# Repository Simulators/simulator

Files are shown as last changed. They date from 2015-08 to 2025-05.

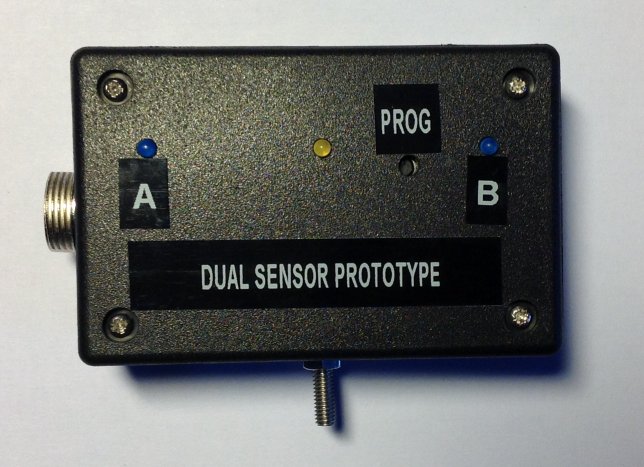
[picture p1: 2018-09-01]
experimental/twinsensor/documentation/Images/Img_0275.jpg

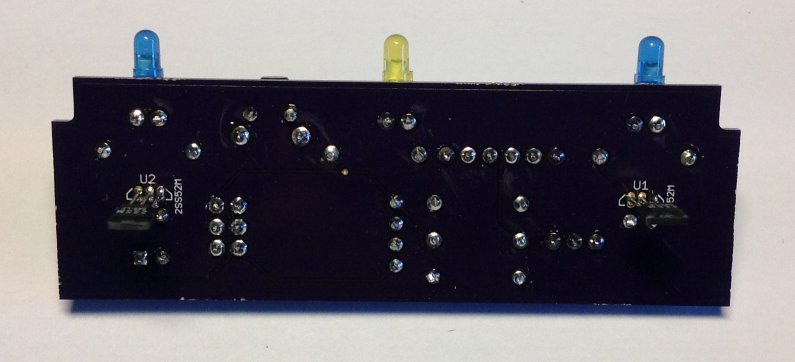
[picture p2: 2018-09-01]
experimental/twinsensor/documentation/Images/Img_0268 (1).jpg

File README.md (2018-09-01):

# simulator
The Liverpool Ringing Simulator Project

<b>The Type 1 simulator is no longer under active development. The repository for the Type 2 simulator is at https://github.com/Simulators/simulator-type2, and you should start there if you are building a new simulator.</b>

Here you will find archived all the resources for building the Liverpool Ringing Simulator Project's original (Type 1) simulator interfaces and sensor heads, including:
* Hardware & Software Manuals
* Firmware Source Code
* Eagle PCB Designs
* PCB Fabrication Gerber Files

If you didn't get here from http://www.simulators.org.uk/, you might want to go and look at that, too.

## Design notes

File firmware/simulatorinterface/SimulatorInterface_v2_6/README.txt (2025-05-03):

*********************************************************************************************
*                 HOW TO USE OPTION X - TURNING OFF DELAYS IN THE INTERFACE                 *
*********************************************************************************************

Type 1 Simulator Interface firmware v2.6 implements a feature to turn off the application of
strike delays in the Simulator Interface, i.e. to use the Type 2 behaviour where delays are
managed within the Simulator Software itself (e.g. Abel).

This feasture has been developed for one particular use case. For most Type 1 users, firmware
v2.5 is still the latest recommended version.

           *** THIS FEATURE DOES NOT APPEAR IN THE TYPE 1 SIMULATOR DOCUMENTATION ***

By default, a Type 1 interface stores and applies the strike delay (from BDC to strike point)
in the interface, receiving the delays from Abel at startup and saving them to EEPROM. CLI
option X turns this off, so that signals are sent to the PC at BDC, not at the strike point,
which is the Type 2 behaviour. To support this, the WAIT_TO_SEND state does double duty
as the post-signal guard timer. 

When application of delays in the interface is turned off, the option to set default timers
(Option Z in Debug Mode) is changed to set to 100ms, the default Type 2 Guard Timer, instead
of 500ms, and saving to EEPROM (Option S) is changed to save the delay timers to EEPROM along
with the other settings. The serial receiver code is also changed to not overwrite the timers
when application of delays is turned off.

To disable application of delay timers in the interface, do the following:
 * Select CLI Option X to toggle the applyDelayTimers flag to FALSE.
 * Select CLI Option D to enable debugging.
 * Select CLI Option Z to set 100ms (10cs) timers.
 * Select CLI Option S to save all this to EEPROM.
 * Reboot the interface with the reset button.
 * Change the Abel configuration to check the box "Abel applies delays (No MBI)".
 
Strike delays will now be applied by Abel, and any delay values sent to the interface will be ignored.

To re-enable application of delay timers in the interface, do the following:
 * Select CLI Option X to toggle the applyDelayTimers flag to TRUE.
 * Select CLI Option S to save this change to EEPROM.
 * Reboot the interface with the reset button.
 * Change the Abel configuration to uncheck the "Abel applies delays (No MBI)" box, and restart Abel.

Abel will now send delay values to the interface, which will store and apply them.

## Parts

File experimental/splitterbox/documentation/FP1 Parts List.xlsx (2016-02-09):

Splitter Box Functional Prototype - Main Parts List
 | Part | Qty | Farnell
 | USB-B-S-RA | 6 | 2112373
 | FT232RL | 6 | 1146032
 | 47pF 2.54mm 50V MLCC | 12 | 1141762
 | 10K | 14 | 9341110
 | 1K | 7 | 9341102
 | LED 3mm Blue | 6 | Ebay
 | 100nF 2.54mm 50V MLCC | 10 | 1457655
 | MAX233EPP+G36/MAX233CPP+G36 | 1 | 2085180 | or 2113688 (not low temp)
 | ATmega328P-PU | 1 | 1715487
 | IC Socket 20 pin | 1 | 2445624
 | IC Socket 28 pin | 1 | 2445626
 | 47uF 2.54mm 25V 6.3mm Elko | 1 | 1870939
 | Omrom PB B3F-1020 | 2 | 1608274
 | BiColor LED 3mm Red/Green 2 Lead | 1 | 1142488 | Prototype was 1581204, now discontinued
 | 10nF 2.54mm 50V MLCC | 1 | 1141772
 | Ferrite BL02RN1R2M2B | 1 | 9526838
 | 0.1" Header Pins | 12 | Ebay

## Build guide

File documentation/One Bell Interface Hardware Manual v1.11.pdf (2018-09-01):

# The Liverpool Ringing Simulator

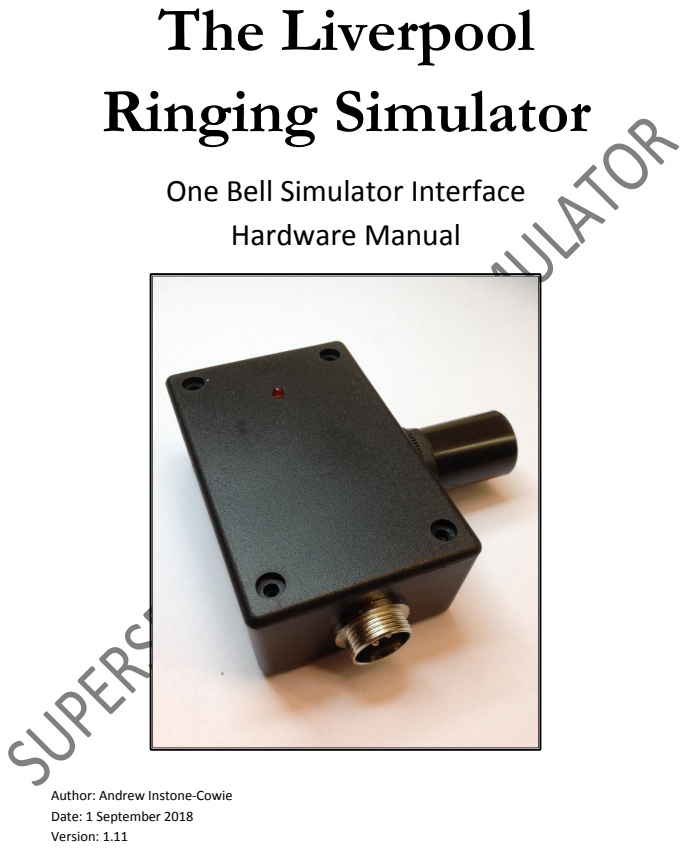
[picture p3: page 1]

One Bell Simulator Interface
Hardware Manual

Author: Andrew Instone-Cowie
Date: 1 September 2018
Version: 1.11

### Contents

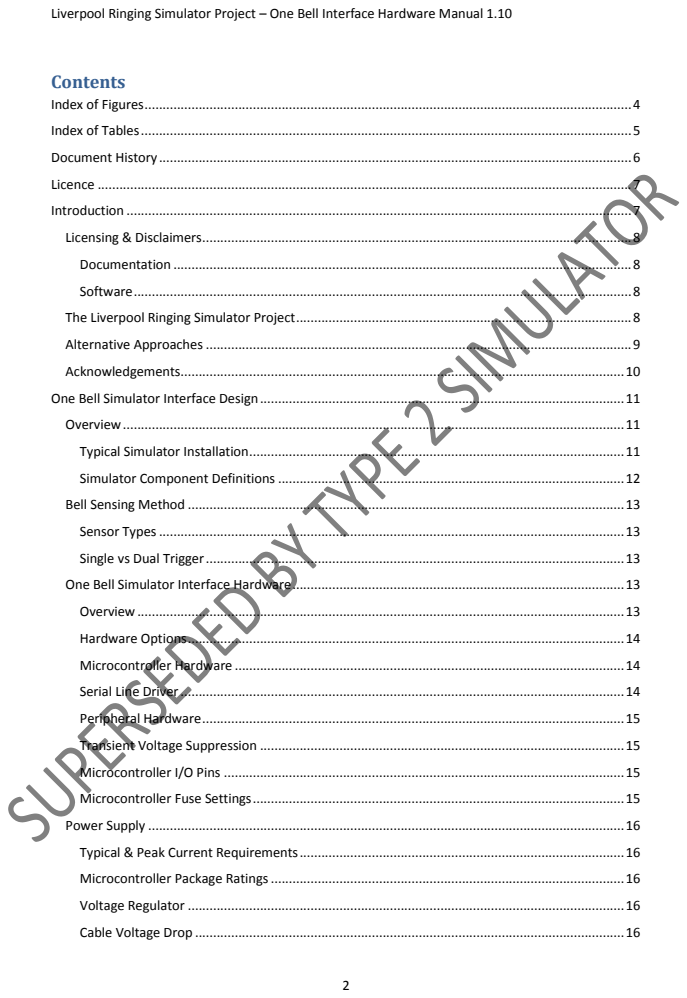
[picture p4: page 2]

Liverpool Ringing Simulator Project – One Bell Interface Hardware Manual 1.10

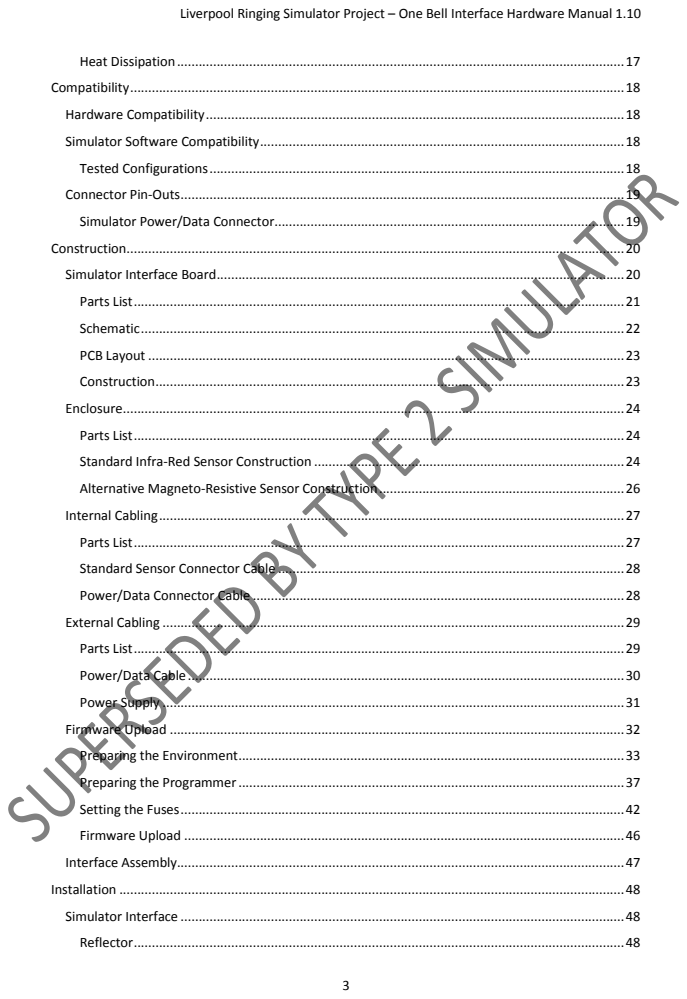
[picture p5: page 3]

### Index of Figures

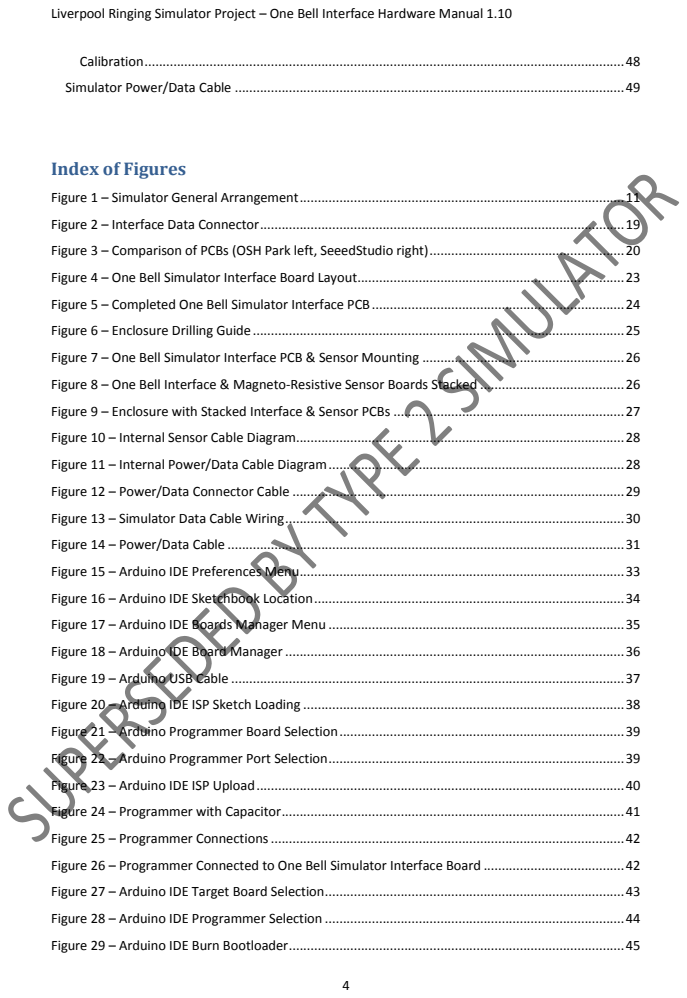
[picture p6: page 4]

Calibration.....................................................................................................................................48
Simulator Power/Data Cable ............................................................................................................49

Figure 1 – Simulator General Arrangement..........................................................................................11
Figure 2 – Interface Data Connector.....................................................................................................19
Figure 3 – Comparison of PCBs (OSH Park left, SeeedStudio right)......................................................20
Figure 4 – One Bell Simulator Interface Board Layout..........................................................................23
Figure 5 – Completed One Bell Simulator Interface PCB......................................................................24
Figure 6 – Enclosure Drilling Guide .......................................................................................................25
Figure 7 – One Bell Simulator Interface PCB & Sensor Mounting ........................................................26
Figure 8 – One Bell Interface & Magneto-Resistive Sensor Boards Stacked ........................................26
Figure 9 – Enclosure with Stacked Interface & Sensor PCBs ................................................................27
Figure 10 – Internal Sensor Cable Diagram...........................................................................................28
Figure 11 – Internal Power/Data Cable Diagram..................................................................................28
Figure 12 – Power/Data Connector Cable ............................................................................................29
Figure 13 – Simulator Data Cable Wiring..............................................................................................30
Figure 14 – Power/Data Cable ..............................................................................................................31
Figure 15 – Arduino IDE Preferences Menu..........................................................................................33
Figure 16 – Arduino IDE Sketchbook Location......................................................................................34
Figure 17 – Arduino IDE Boards Manager Menu ..................................................................................35
Figure 18 – Arduino IDE Board Manager ..............................................................................................36
Figure 19 – Arduino USB Cable .............................................................................................................37
Figure 20 – Arduino IDE ISP Sketch Loading .........................................................................................38
Figure 21 – Arduino Programmer Board Selection...............................................................................39
Figure 22 – Arduino Programmer Port Selection..................................................................................39
Figure 23 – Arduino IDE ISP Upload......................................................................................................40
Figure 24 – Programmer with Capacitor...............................................................................................41
Figure 25 – Programmer Connections..................................................................................................42
Figure 26 – Programmer Connected to One Bell Simulator Interface Board .......................................42
Figure 27 – Arduino IDE Target Board Selection...................................................................................43
Figure 28 – Arduino IDE Programmer Selection ...................................................................................44
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

### Index of Tables

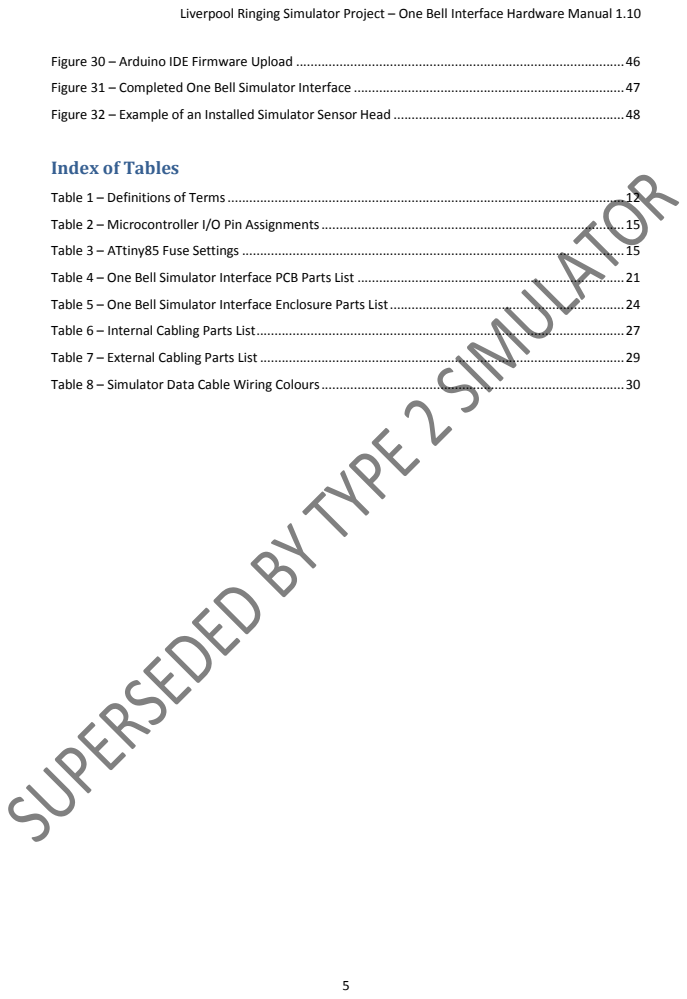
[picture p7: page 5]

Figure 30 – Arduino IDE Firmware Upload ...........................................................................................46
Figure 31 – Completed One Bell Simulator Interface ...........................................................................47
Figure 32 – Example of an Installed Simulator Sensor Head ................................................................48

Table 1 – Definitions of Terms..............................................................................................................12
Table 2 – Microcontroller I/O Pin Assignments....................................................................................15
Table 3 – ATtiny85 Fuse Settings..........................................................................................................15
Table 4 – One Bell Simulator Interface PCB Parts List ..........................................................................21
Table 5 – One Bell Simulator Interface Enclosure Parts List.................................................................24
Table 6 – Internal Cabling Parts List......................................................................................................27
Table 7 – External Cabling Parts List .....................................................................................................29
Table 8 – Simulator Data Cable Wiring Colours....................................................................................30

### Document History

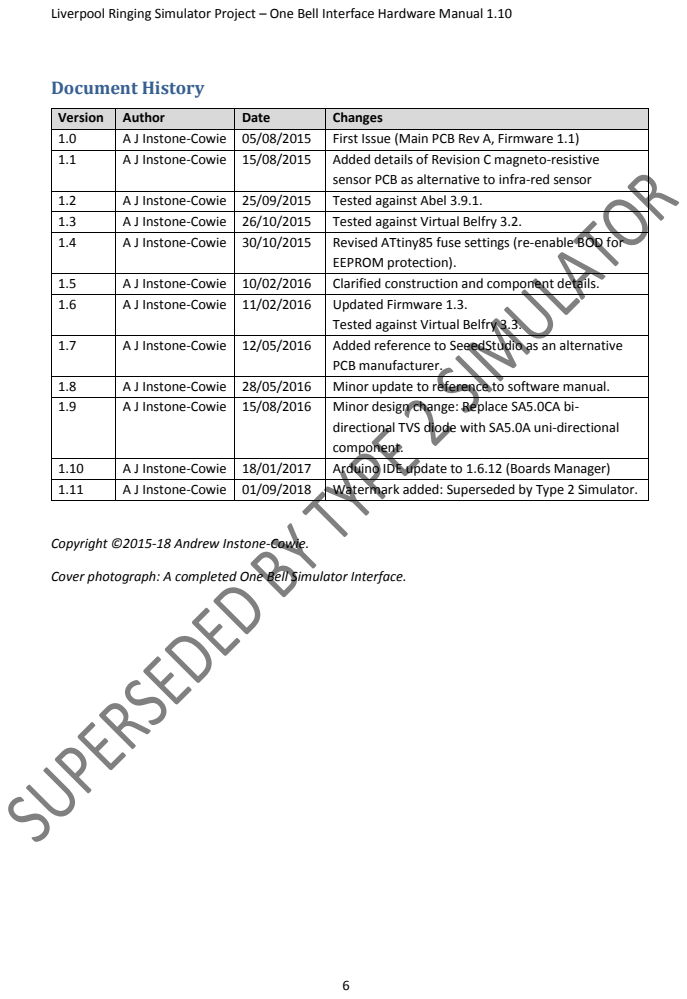
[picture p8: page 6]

Version | Author | Date | Changes
1.0 | A J Instone-Cowie | 05/08/2015 | First Issue (Main PCB Rev A, Firmware 1.1)
1.1 | A J Instone-Cowie | 15/08/2015 | Added details of Revision C magneto-resistive sensor PCB as alternative to infra-red sensor

1.2 | A J Instone-Cowie | 25/09/2015 | Tested against Abel 3.9.1.
1.3 | A J Instone-Cowie | 26/10/2015 | Tested against Virtual Belfry 3.2.
1.4 | A J Instone-Cowie | 30/10/2015 | Revised ATtiny85 fuse settings (re-enable BOD for EEPROM protection).

1.5 | A J Instone-Cowie | 10/02/2016 | Clarified construction and component details.
1.6 | A J Instone-Cowie | 11/02/2016 | Updated Firmware 1.3. Tested against Virtual Belfry 3.3.

1.7 | A J Instone-Cowie | 12/05/2016 | Added reference to SeeedStudio as an alternative PCB manufacturer.

1.8 | A J Instone-Cowie | 28/05/2016 | Minor update to reference to software manual.
1.9 | A J Instone-Cowie | 15/08/2016 | Minor design change: Replace SA5.0CA bi-directional TVS diode with SA5.0A uni-directional component.

1.10 | A J Instone-Cowie | 18/01/2017 | Arduino IDE update to 1.6.12 (Boards Manager)
1.11 | A J Instone-Cowie | 01/09/2018 | Watermark added: Superseded by Type 2 Simulator.

Copyright ©2015-18 Andrew Instone-Cowie.

Cover photograph: A completed One Bell Simulator Interface.

### Licence

This work is licensed under a Creative Commons Attribution-ShareAlike 4.0 International License.¹

Unless otherwise separately undertaken by the Licensor, to the extent possible, the Licensor offers the Licensed Material as-is and as-available, and makes no representations or warranties of any kind concerning the Licensed Material, whether express, implied, statutory, or other. This includes, without limitation, warranties of title, merchantability, fitness for a particular purpose, non-infringement, absence of latent or other defects, accuracy, or the presence or absence of errors, whether or not known or discoverable. Where disclaimers of warranties are not allowed in full or in part, this disclaimer may not apply to You.

To the extent possible, in no event will the Licensor be liable to You on any legal theory (including, without limitation, negligence) or otherwise for any direct, special, indirect, incidental, consequential, punitive, exemplary, or other losses, costs, expenses, or damages arising out of this Public License or use of the Licensed Material, even if the Licensor has been advised of the possibility of such losses, costs, expenses, or damages. Where a limitation of liability is not allowed in full or in part, this limitation may not apply to You.

### Introduction

This Hardware Manual describes the design and construction of the hardware for a ringing Simulator Interface which allows a sensor, attached to a real tower bell or teaching dumb bell, to be connected to a computer Simulator Software Package such as Abel²

, Beltower³ or Virtual Belfry⁴ .

- Parts lists and schematics are provided. Links are also provided to suggested sources of parts, including ready-made printed circuit boards.
- Links are provided to the associated firmware source code, PCB CAD files and other supporting data hosted on GitHub.
- Details of the design and configuration of the interface firmware, and the configuration and operation of popular simulator packages, are covered in the accompanying Software Manual.
- Designs and construction details for a range of sensors are also covered separately.
- This is a build-it-yourself project. No pre-built hardware is available.

This design is derived from the Liverpool Ringing Simulator Project Simulator Interface, a separate Hardware Manual for which is available, and which contains more details of the background to the project and the design of the interfaces.

1 http://creativecommons.org/licenses/by-sa/4.0/2 http://www.abelsim.co.uk/
3 http://www.beltower.co.uk/
4 http://www.belfryware.com/

### Licensing & Disclaimers

Documentation
All original manuals and other documentation (including PCB layout CAD files and schematics) released as part of the Liverpool Ringing Simulator Project⁵ are released under the Creative Commons Attribution-ShareAlike 4.0 International License (CC BY-SA),⁶ which includes the following disclaimers:

Unless otherwise separately undertaken by the Licensor, to the extent possible, the Licensor offers the Licensed Material as-is and as-available, and makes no representations or warranties of any kind concerning the Licensed Material, whether express, implied, statutory, or other. This includes, without limitation, warranties of title, merchantability, fitness for a particular purpose, non-infringement, absence of latent or other defects, accuracy, or the presence or absence of errors, whether or not known or discoverable. Where disclaimers of warranties are not allowed in full or in part, this disclaimer may not apply to You.

To the extent possible, in no event will the Licensor be liable to You on any legal theory (including, without limitation, negligence) or otherwise for any direct, special, indirect, incidental, consequential, punitive, exemplary, or other losses, costs, expenses, or damages arising out of this Public License or use of the Licensed Material, even if the Licensor has been advised of the possibility of such losses, costs, expenses, or damages. Where a limitation of liability is not allowed in full or in part, this limitation may not apply to You.

Software
All original software released as part of the Liverpool Ringing Simulator Project is released under the GNU General Public Licence (GPL), Version 3⁷
, and carries the following disclaimers:

This program is free software: you can redistribute it and/or modify it under the terms of the GNU General Public License as published by the Free Software Foundation, either version 3 of the License, or (at your option) any later version.

This program is distributed in the hope that it will be useful, but WITHOUT ANY WARRANTY; without even the implied warranty of MERCHANTABILITY or FITNESS FOR A PARTICULAR PURPOSE. See the GNU General Public License for more details.

### The Liverpool Ringing Simulator Project

The Liverpool Ringing Simulator Project is based on work undertaken at Liverpool Cathedral to provide a 12-bell simulator for demonstration and training purposes. More details of the background to and objectives of the project can be found in the accompanying Software Manual, or in the main Simulator Interface Hardware Manual.

The use of simulators has great potential in the training of new ringers, and therefore the Liverpool Ringing Simulator Project seeks to promote the installation and take-up of simulators as a teaching

5 http://www.simulators.org.uk
6 http://creativecommons.org/licenses/by-sa/4.0/7 http://www.gnu.org/licenses/gpl-3.0.en.html aid in other towers. The project presents the work undertaken at the Cathedral, and other towers, and makes it freely available for ringers to build and install simulators at relatively low cost.

### Alternative Approaches

Other approaches to connecting a single bell to a simulator software package are possible:

- For small numbers of bells, over relatively short cable distances, the approach of using RS-232 control lines as input signals, as described in the Abel and Beltower documentation, is feasible⁸
. The downsides of this approach are that modern PCs usually have not more than one (if any) RS-232 serial port, limiting the number of bells which may be connected; and that multiple long cable runs are required between the simulator PC and bell sensor heads.
- The Bagley Single Bell Interface (SBI), complete with sensor head and cabling, is available from David Bagley as an off-the-shelf commercial solution⁹
. This approach is probably the best option for a tower wanting a professionally designed and manufactured, vendor supported simulator solution with minimal technical input. This solution is considerably more expensive than the DIY interface described in this document (and associated Sensor Heads described separately), and its designs and operating software are not published.
- A simulator sensor solution based on wireless sensors¹⁰ is under development. As currently designed this has some disadvantages over a wired installation (such as the need to switch sensor power on and off by hand, and the need for regular sensor battery recharging), but this approach has promise for mobile use. The system is also closed source, and designs and operating software are not published.

8 http://www.abelsim.co.uk/doc/spconn.htm
9 http://www.ringing.demon.co.uk/abel/abelface.htm 10 http://www.belfree.co.uk/

### Acknowledgements

The Liverpool Ringing Simulator Project relies extensively on work already undertaken by others, notably David Bagley (developer of the Bagley MBI), Chris Hughes and Simon Feather (developers of the Abel simulator software package), Derek Ballard (developer of the Beltower simulator software package), Doug Nichols (developer of the Virtual Belfry simulator software package), and others. Their invaluable contributions are hereby acknowledged. Sources used are referenced in the

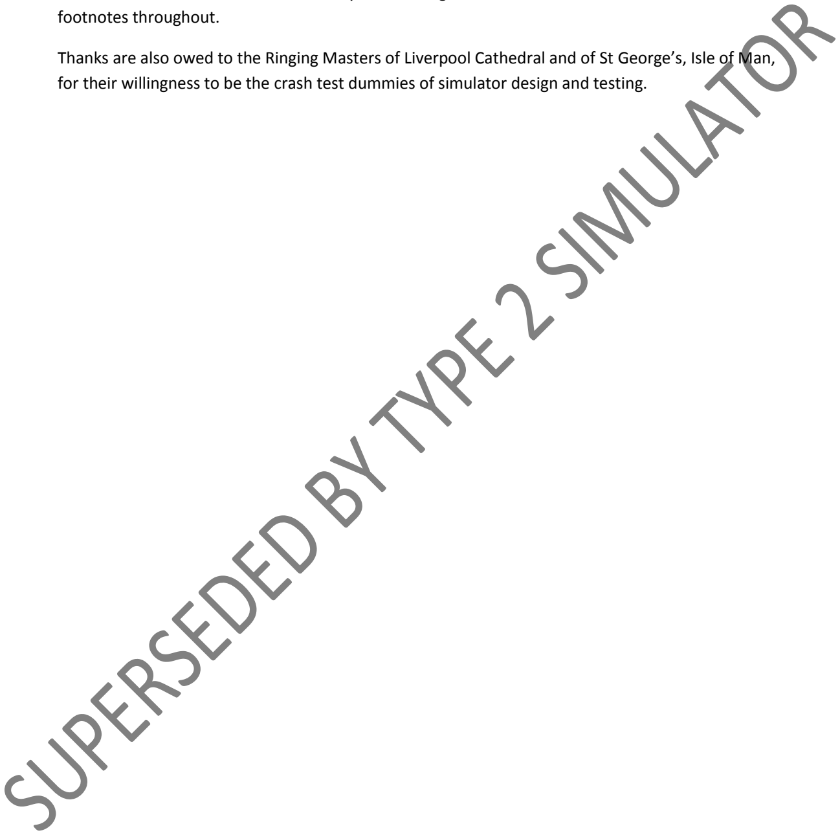
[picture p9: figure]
footnotes throughout.

Thanks are also owed to the Ringing Masters of Liverpool Cathedral and of St George’s, Isle of Man, for their willingness to be the crash test dummies of simulator design and testing.

### One Bell Simulator Interface Design

### Overview

Typical Simulator Installation
The following diagram illustrates the general arrangement of a Simulator installation using the One Bell Simulator Interface.

An integrated Sensor Head and Simulator Interface (the One Bell Simulator Interface) is located in the belfry. A single data cable transmits the signal from the One Bell Simulator Interface to the Simulator PC, using a mutually agreed protocol. The same cable feeds power from a low voltage power supply in the ringing room back up to the belfry to power the One Bell Simulator Interface.

In the ringing room, a PC runs a Simulator Software Package which interprets the received signals and turns them into the simulated sound of a bell.

Figure 1 – Simulator General Arrangement

This manual describes the design and construction of the One Bell Simulator Interface hardware component of the Simulator. An accompanying Software Manual describes the Simulator Interface firmware, and the configuration of popular Simulator Software Packages.

A separate Hardware Manual is available which describes the design and construction of a Simulator Interface which supports the installation of sensors on up to 12 bells.

Simulator Component Definitions
Within this document the following terms are used as defined in the table below:

Table 1 – Definitions of Terms

Term | Definition
Sensor Head | A Sensor Head detects the position of a real bell (or a dumb bell) at the bottom of its swing, and sends a signal at that time to the Simulator Interface. Multiple Sensor Heads may be installed, one for each bell to be connected to the Simulator.
Simulator Interface | The Simulator Interface aggregates the incoming signals from the Sensor Heads, and relays the signals to the Simulator PC (or to a Hardware Simulator) over a single consolidated data connection. The Simulator Interface applies a configurable delay to each signal so that it is received by the Simulator at the time the clapper of a real bell would have struck.
One Bell Simulator Interface | A single Sensor Head and a Simulator Interface integrated into a single unit, for use with a single tower bell or dumb bell.
Simulator Data Connection | The Simulator Interface is connected to the Simulator over a single power/data connection. For compatibility with existing installations and software, the Liverpool Ringing Simulator project Simulator Interface uses a RS-232 serial data link running at 2400 bps. The cable carrying the Simulator/Power Data Connection is also used to supply power to the Simulator Interface and Sensor Heads from a low-voltage power supply located in the ringing room.
Simulator Interface Protocol | The Simulator Interface communicates with the Simulator over the Data Connection using a mutually agreed logical protocol. For compatibility with existing installations and software, the Liverpool Ringing Simulator project Simulator Interface implements the core Bagley MBI Protocol, with additional extensions for debugging and configuration purposes. These extensions are described in the accompanying Software Manual.
Simulator | Collectively, the combination of a Simulator Software Package running on a Simulator PC; or alternatively a dedicated Hardware Simulator device fulfilling the same function.
Simulator Software Package | The Simulator Software Package produces the sound of simulated change ringing through loudspeakers and/or headphones, in response to input signals from the Simulator Interface and its own internal instructions, method definitions, etc. The Liverpool Ringing Simulator project Simulator Interface has been tested with a number of popular Simulator Software Packages. These are listed below, and details of configuration can be found in the accompanying Software Manual.
Simulator PC | The Simulator PC is a general purpose computing platform which runs a Simulator Software Package, typically an Intel-compatible PC running a version of Microsoft Windows. At least one RS-232 serial port (or a USB to RS-232 adapter) is required for the Simulator Data Connection, and loudspeakers or headphones.

Hardware Simulator A Hardware Simulator is a dedicated stand-alone proprietary device which fulfils both the hardware and software functions of a Simulator. An example of a Hardware Simulator is the Bagley Ringleader Simulator¹¹. This device has not been available for new supply for some years.

### Bell Sensing Method

A fuller discussion of these topics can be found in the main Simulator Interface Hardware Manual.

Sensor Types
Over the years a number of different approaches have been used for detecting the position of a tied or dumb bell, and translating that position into a signal for use by a Simulator.
- This design uses an optical sensor, using the low cost commercially available modulating infra-red detector adopted as the project standard.
- An alternative construction using a PCB developed for the magneto-resistive Sensor Head is also documented

Single vs Dual Trigger
There are generally two approaches used by Simulators when detecting signals from Sensor Heads:
- The dual trigger approach uses two triggers (for example, optical reflectors) on the shroud of the wheel of each bell, one of which triggers at the moment that the bell would strike at handstroke, the other at the moment that the bell would strike at backstroke
- The second approach is to use a single trigger, which triggers as the bell passes through the bottom dead centre of its swing. A delay is then applied before the Simulator triggers the simulated sound of the bell. Work by John Norris¹² has shown that this approach can provide an acceptable degree of accuracy, with any errors considered too small to be detectable to the human ear.

The Liverpool Ringing Simulator Project One Bell Simulator Interface adopts the single trigger approach, on the grounds of simplicity of installation and compatibility with other similar systems. This is discussed in more detail in the accompanying Software Manual.

### One Bell Simulator Interface Hardware

Overview
The One Bell Simulator Interface hardware consists of three main functional blocks:
- A 5V regulated power supply, which provides power for the interface electronics and for the Sensor Head.
- A digital microcontroller, which detects incoming signals from the Sensor Head, applies a configurable delay, and then sends a signal to the Simulator PC in the form of a stream of ASCII characters.

11 http://www.ringing.demon.co.uk/ringleader/ringleader.htm 12 http://www.jrnorris.co.uk/strike.html

- A RS-232 serial line driver, which converts the TTL-level signals from the microcontroller to higher voltage RS-232 signals, for transmission over longer distances to the Simulator PC.

All the components of these functional blocks are mounted on a single custom PCB, together with diagnostic LED, and all components are mounted in a robust enclosure with a standardised connector for the Simulator Power/Data Connection.

Eagle CAD and Gerber files are available in the GitHub repository, and links to a low-volume PCB fabricator are provided in the Construction section.

Hardware Options
In common with the main Simulator Interface, the use of the same Atmel AVR microcontroller family has been continued for the One Bell Simulator Interface, allowing the same tool chain to be used for code development and deployment, and re-use of much of the firmware code.

Microcontroller Hardware
The One Bell Simulator Interface uses the Atmel ATtiny85 microcontroller.
- The ATtiny85 is an 8-pin device with a much smaller footprint than the ATmega328P used in the main Simulator Interface. This allows the overall interface PCB size to be reduced, so that the PCB can be accommodated in the same enclosure adopted as the project standard for Sensor Heads.
- The One Bell Simulator Interface makes use of the ATtiny85’s internal 8MHz oscillator. Although this is less accurate than an external oscillator, the internal oscillator is still adequate for the purposes of the interface, and this reduces the overall component count and complexity of the interface board by omitting a crystal and load capacitors.
- Although the One Bell Simulator Interface uses the Arduino development tool chain, it does not use the Arduino boot loader program. The ATtiny85 is programmed via an ICSP header using a programmer (the Arduino-as-ISP method is suggested, and is described in more detail in the Construction section of this manual.)
- Unlike the ATmega328P, the ATtiny85 does not have a hardware serial UART. The serial port is therefore emulated in the One Bell Simulator Interface firmware, using the standard Arduino SoftwareSerial library.

Serial Line Driver
The Simulator Interface uses the Maxim MAX233 RS-232 serial line driver¹³. The MAX233 has the advantage over other line driver ICs of requiring no external charge pump capacitors, also reducing the overall component count.

13 http://www.maximintegrated.com/en/products/interface/transceivers/MAX233.html

Peripheral Hardware
A single diagnostic LED is included to provide visual status information on the activity of the One Bell Simulator Interface, because of the difficulty of using the serial interface for this purpose. This is optional, but recommended.

Transient Voltage Suppression
The One Bell Simulator Interface uses a Transient Voltage Suppression (TVS) diode to provide a degree of protection against induced over-voltages on the power supply lines, for example resulting from local lightning strikes (similar devices are included in the main Simulator Interface and Sensor Head designs).

Microcontroller I/O Pins
The following table shows the ATtiny85 pin assignments for the One Bell Simulator Interface:

Table 2 – Microcontroller I/O Pin Assignments

Arduino I/O Pin¹⁴ | ATtiny85 Physical Pin | Function
0 | 5 | Red Diagnostic LED
1 | 6 | (Spare)
2 | 7 | Bell Sensor
3 | 2 | Serial Port Transmit
4 | 3 | Serial Port Receive

Microcontroller Fuse Settings
The ATtiny85 microcontroller has a number of configuration registers known as fuses. These are used to control the behaviour of the microcontroller¹⁵. Fuse values are contained in the file boards.txt described in the section on uploading firmware below, and are only written during the burn bootloader phase of programming.

Warning: Setting incorrect fuse values can render the microcontroller unusable or prevent further reprogramming without specialist hardware.

The fuse values for the One Bell Simulator Interface are defined in the following table.

Table 3 – ATtiny85 Fuse Settings

Fuse | Value | Notes
Low | 0xE2 | 8MHz internal oscillator, maximum clock startup delay.
High | 0XD5 | Enable serial programming, preserve EEPROM contents, Brown-out detection level 1 (2.7V).

For more details of these fuse settings and their functions, refer to the ATtiny85 data sheet, or see the online fuse calculator at: http://eleccelerator.com/fusecalc/fusecalc.php?chip=attiny85&LOW=E2&HIGH=D7&EXTENDED=FF&LOCKBIT=FF. (http://eleccelerator.com/fusecalc/fusecalc.php?chip=attiny85&LOW=E2&HIGH=D7&EXTENDED=FF&LOCKBIT=FF)

14 Pin numbers as referenced in the Arduino programming environment.
15 Fuse tutorial (based on ATmega328P): http://www.martyncurrey.com/arduino-atmega-328p-fuse-settings/

### Power Supply

DC power is supplied to the One Bell Simulator Interface over the Power/Data Cable at a higher voltage than required, to overcome the effects of losses due the resistance of the cable. Incoming power is fed to a conventional linear 5V regulator on the One Bell Simulator Interface PCB. A small TO-92 case voltage regulator is used to reduce the overall PCB footprint.

Typical & Peak Current Requirements
The One Bell Simulator Interface main board and sensor all operate at 5V DC. The typical total power requirement with a standard infra-red optical sensor is approximately 34mA, with the sensor not triggered. However the sensor draws more current when in the triggered state, mainly because the infra-red detector used includes a small internal status LED. The peak power requirement with the sensor in the triggered state is approximately 42mA. This is within the 100mA maximum current rating of the 78L05 5V voltage regulator.

The alternative magneto-resistive sensor draws only approximately 7mA, compared to the approximately 25mA of the standard infra-red sensor.

Microcontroller Package Ratings
The Atmel ATtiny85 microcontroller has an absolute source/sink current limit of 40mA per pin, and a total device package current limit of 200mA. The recommended total IO port current is 60mA. The sensor input pin was measured to sink approximately 130 μA when triggered. Other pins drive the diagnostic LED and the RS-232 line driver, and in total these do not draw more than a few milliamps, so the microcontroller limits do not present a problem.

Voltage Regulator
The Simulator Interface uses a standard linear voltage regulator to provide a regulated 5V DC supply. The voltage regulator requires an input supply of at least 7V DC in order to maintain a stable 5V DC output. The voltage regulator is fed via a polarity protection diode, which drops approximately 0.7V, giving a minimum input voltage requirement of 7.7V at the One Bell Simulator Interface input.

Cable Voltage Drop
The cable suggested for the main Simulator Power/Data Connection has a specified maximum resistance of 92Ω/km/core, or 0.092Ω /m/core¹⁶
. For example, the actual resistance of the (two) power supply cores of the 24m Simulator Data Connection cable used at Liverpool Cathedral was found to be 4.08Ω, or 0.085Ω/m/core, within the stated specification.

As an example, at an actual peak supply current of 42mA, this would result in a voltage drop of 0.17V along the 24m of cable, and therefore a theoretical minimum supply voltage to the cable of 7.87V in order for the voltage regulator to maintain a stable 5V DC output. In practice a multi-voltage DC plug-in power supply unit rated at 1000mA with the output set to 9V has been found adequate for a cable runs up to 25m. (Cable voltage drop has a greater impact on larger Sensor Interfaces with large numbers of Sensor Heads.)

16 http://www.rapidonline.com/pdf/02-0260.pdf

Heat Dissipation
At peak load, with a current requirement of 42mA, the voltage regulator would be dissipating a minimum¹⁷ of approximately 84mW. The dissipation will be higher with shorter cable runs or a higher supply voltage; for example with a 9V supply the dissipation would be up to 130mW. The data sheet for the voltage regulator indicates that this will not require a heatsink.

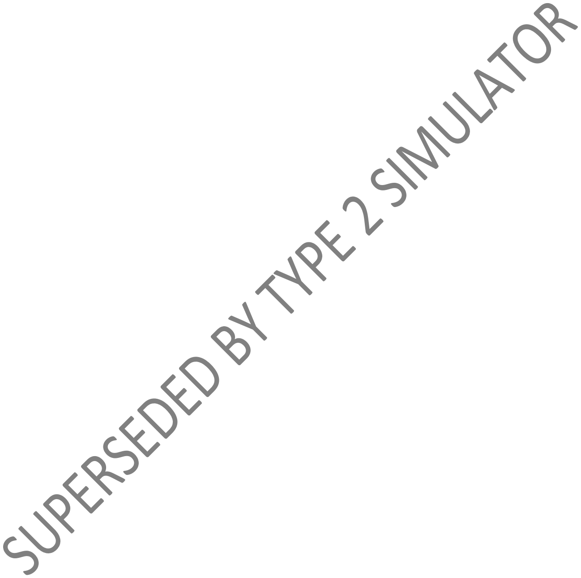
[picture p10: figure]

17 Assuming the minimum required input voltage of 7V at the voltage regulator.

### Compatibility

### Hardware Compatibility

The One Bell Simulator Interface has been designed to be compatible, as far as possible, with existing simulator hardware, to allow operation with unmodified Simulator Software Packages which support the MBI protocol. This is described in more detail in the accompanying Software Manual.

To maximise compatibility and interoperability, the Simulator Data Connection uses a RS-232 data link to the Simulator, running at 2400 bps, 8 data bits, 1 stop bit, no parity.

The Simulator Data Connection connector of the One Bell Simulator Interface uses a 5-way locking GX16-5 connector, although constructors are free to adopt whatever connector standards they wish. The use of physically compatible connectors with incompatible wiring conventions is strongly discouraged.

### Simulator Software Compatibility

Tested Configurations
The One Bell Simulator Interface has been tested successfully with the following Simulator Software Packages:
- Abel 3.9.1
- Beltower 2015 (12.29)
- Virtual Belfry¹⁸ 3.4

This is described in more detail in the accompanying Software Manual.

18 3.1b is the minimum version of Virtual Belfry required for proper handling of interfaces of this type.

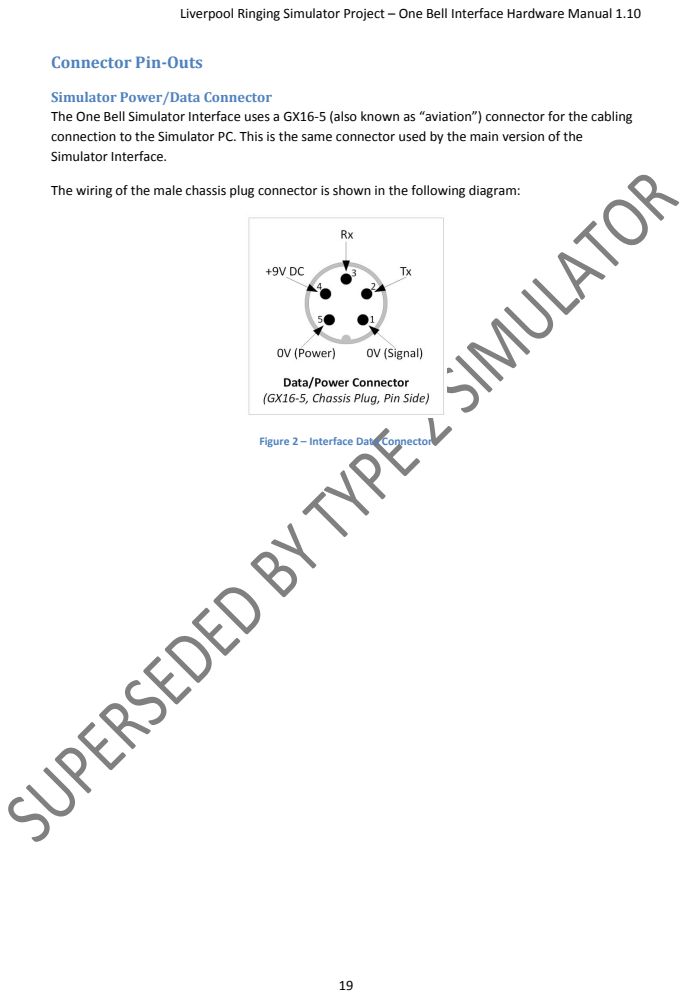
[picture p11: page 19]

Connector Pin-Outs

Simulator Power/Data Connector
The One Bell Simulator Interface uses a GX16-5 (also known as “aviation”) connector for the cabling
connection to the Simulator PC. This is the same connector used by the main version of the
Simulator Interface.

The wiring of the male chassis plug connector is shown in the following diagram:

Figure 2 – Interface Data Connector

### Construction

The following sections describe the construction of the One Bell Simulator Interface.

### Simulator Interface Board

The One Bell Simulator Interface Board contains the power supply for the interface and sensor, the microcontroller, a RS-232 serial line driver, a diagnostic LED, and an ICSP¹⁹ programming interface for firmware upload.

Eagle CAD and Gerber files for the board can be downloaded from GitHub. Gerber files are provided for two possible board manufacturers, OSH Park in the USA and SeeedStudio in China.

- https://github.com/Simulators/simulator/tree/master/hardware/onebellinterface
- https://oshpark.com/shared_projects/oq0CJlkk
- http://www.seeedstudio.com

Both manufacturers have been found to supply boards of a high quality, although the Chinese boards are of a slightly lower specification (e.g. HASL finish rather than ENIG) but are considerably cheaper in quantity.

Sample boards from both manufacturers are shown in the following photograph.

Figure 3 – Comparison of PCBs (OSH Park left, SeeedStudio right)

19 In-Circuit Serial Programming

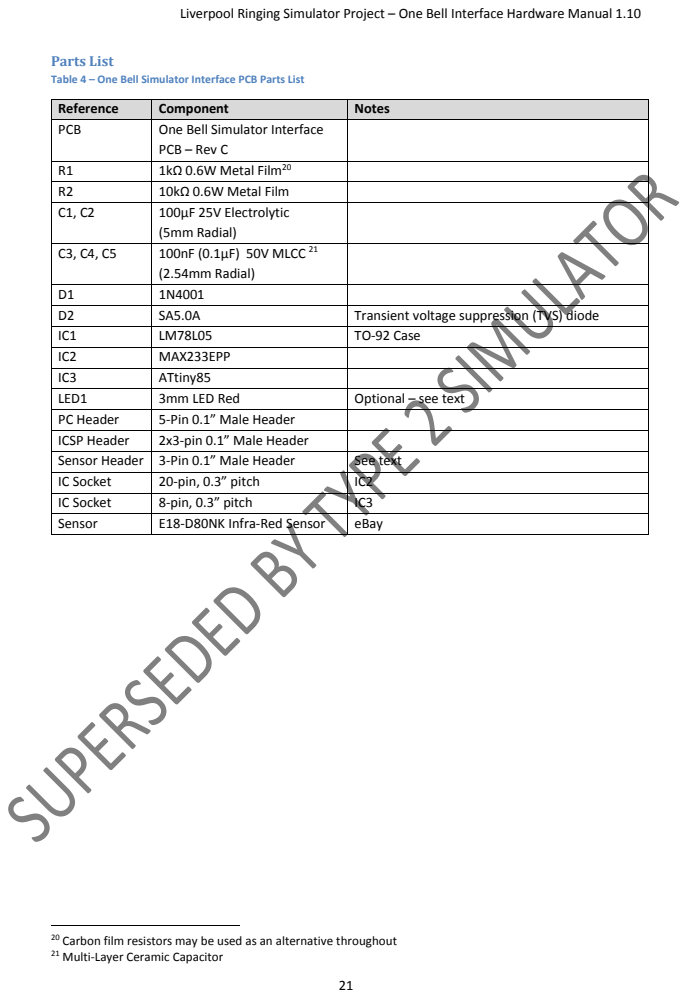
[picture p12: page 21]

Parts List
Table 4 – One Bell Simulator Interface PCB Parts List

Reference | Component | Notes
PCB | One Bell Simulator Interface PCB – Rev C

R1 | 1kΩ 0.6W Metal Film²⁰
R2 | 10kΩ 0.6W Metal Film
C1, C2 | 100µF 25V Electrolytic (5mm Radial)

C3, C4, C5 | 100nF (0.1µF) 50V MLCC ²¹ (2.54mm Radial)

D1 | 1N4001
D2 | SA5.0A | Transient voltage suppression (TVS) diode
IC1 | LM78L05 | TO-92 Case
IC2 | MAX233EPP
IC3 | ATtiny85
LED1 | 3mm LED Red | Optional – see text
PC Header | 5-Pin 0.1” Male Header
ICSP Header | 2x3-pin 0.1” Male Header
Sensor Header | 3-Pin 0.1” Male Header | See text
IC Socket | 20-pin, 0.3” pitch | IC2
IC Socket | 8-pin, 0.3” pitch | IC3
Sensor | E18-D80NK Infra-Red Sensor | eBay

20 Carbon film resistors may be used as an alternative throughout
21 Multi-Layer Ceramic Capacitor

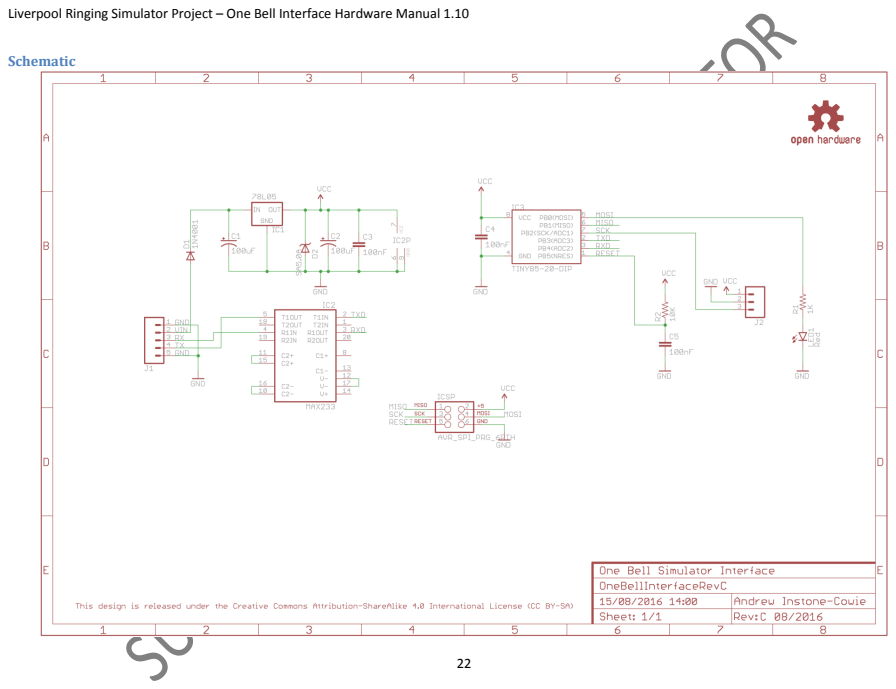
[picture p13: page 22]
Schematic

PCB Layout
The following diagram shows the layout of the One Bell Simulator Interface PCB.

Figure 4 – One Bell Simulator Interface Board Layout

Construction
For use with the standard infra-red sensor, all the components on the One Bell Simulator Interface Board are mounted on top, silkscreen, side of the board.
- Start by soldering the components with the lowest profile (resistors, ceramic capacitors), then the remainder of the components in order of increasing height, ending with the electrolytic capacitors and header pins.
- The use of IC sockets for IC2 & IC3 is optional, but strongly recommended.
- Fitting the diagnostic LED is optional, but strongly recommended. The LED is polarised, and must be mounted in the correct orientation with the cathode on the right. The cathode is usually denoted by a flat on the side of the moulding and by a shorter leg.
- Before fitting the socketed ICs, connect the board to a power supply and check that +5V and 0V appear on the correct pins of the sockets and on the correct header pins. Disconnect the power supply and fit the ICs.
- If the board is powered up at this point, there will be no indication from the diagnostic LED. This is normal if the firmware has not yet been uploaded to the microcontroller.
- Note that if the board is to be used with the alternative stackable magneto-resistive sensor board, then the sensor pins should be mounted on the reverse of the interface board, as illustrated below.
- Pay particular attention to the correct orientation of the polarised components D1, D2, C1, C2, IC1, IC2 & IC3²²

22 Note that prior to PCB Rev C, D2 was a non-polarised component.

A completed One Bell Simulator Interface PCB is shown in the following photograph. Note that this is an earlier version of the PCB.

Figure 5 – Completed One Bell Simulator Interface PCB

### Enclosure

The suggested enclosure for the One Bell Simulator Interface is the WCAH 2855 black ABS box manufactured by Wisher Enterprise Co Ltd.

- This enclosure can be obtained from Maplin, ESR Components and Velleman, and is the same enclosure adopted as a standard for Sensor Heads across the Liverpool Ringing Simulator Project.
- The enclosure is 85mm x 55mm x 30mm (external) overall.

Parts List
Table 5 – One Bell Simulator Interface Enclosure Parts List
Component | Notes
WCAH 2855 ABS Black Enclosure | ESR Components 400-595, Maplin BZ72P, Velleman WCAH2855
No2 x 9mm Stainless Steel Self Tapping Screws | eBay
30mm x 20mm (Diameter) Black Plastic Conduit

Standard Infra-Red Sensor Construction
The following diagram gives a suggested drilling layout for the enclosure.
- Drilling large diameter holes with twist drills can result in bit grabbing and damage to the enclosure. Small diameter (16mm/18mm) hole saws are available at relatively low cost (e.g. on eBay), and these make the process of drilling the enclosure much easier and safer.
- Using a sharp chisel, carefully and gently remove the PCB ribs from the inside of the enclosure as indicated on the diagram below, to allow the Sensor and Power/Data connector to be mounted. Using too much force is likely to crack the case.
- It is recommended that the lid retaining screws supplied with the enclosure are replaced with stainless steel equivalents.
- The 4.5mm mounting hole is optional. Other mounting arrangements may be devised.

- The 3mm hole for the LED is not required if the diagnostic LED is omitted or is mounted flush with the PCB.

WCAH 2855 Enclosure

Figure 6 – Enclosure Drilling Guide

PCB Mounting
The One Bell Simulator Interface PCB is designed to be mounted in the uppermost set of PCB ribs inside the enclosure, as illustrated in the diagram above.

Sensor Mounting
The standard infra-red sensor is mounted through the side of the enclosure using the plastic nuts supplied with the sensor. These should be tightened finger-tight only; do not use tools.

Once the sensor is installed, lightly file or sand the exposed threads so that the masking tube is a firm tight push fit on the end of the sensor.

The following photograph shows the PCB and Sensor mounted in the enclosure, and the internal cabling of the unit.

Figure 7 – One Bell Simulator Interface PCB & Sensor Mounting

Alternative Magneto-Resistive Sensor Construction
As an alternative to the standard infra-red sensor, a design for a version (Type 2) of the magneto-resistive sensor PCB is available. This is described in detail in the Simulator Sensors Hardware Manual, and Eagle CAD and Gerber files for the board can be downloaded from GitHub.

Type 2 of the magneto-resistive sensor PCB is designed to fit into the same enclosure as the One Bell Simulator Interface PCB, and connect to it by means of a 3-pin stacking header. The sensor pins on the interface PCB are mounted on the reverse of the board, and mate with a connector on the sensor PCB. The following photograph shows the stacked boards.

Figure 8 – One Bell Interface & Magneto-Resistive Sensor Boards Stacked

PCB Mounting
The stacked pair of PCBs can be slotted into the PCB mounting ribs of the project standard WCAH 2855 enclosure, as shows in the following photograph.

Figure 9 – Enclosure with Stacked Interface & Sensor PCBs

### Internal Cabling

Two internal cables are required within the One Bell Simulator Interface enclosure, to connect the interface board to the external power/data connector, and to connect the infra-red sensor to the interface board:

- Sensor Connector Cable (standard infra-red sensor only)
- Power/Data Cable

Parts List
Table 6 – Internal Cabling Parts List
Component | Notes
GX16-5 Chassis Plug (Male) | Power/Data Connector
Heat Shrink Sleeving 2.5mm Un-shrunk Size
Ribbon Cable
DuPont 0.1” Female Crimp Connectors | 8
DuPont 0.1” Female Connector Shells | 1 x 5-pin, 1 x 3-pin
While it is possible to make up the DuPont connector cables by hand, this is time consuming and not easy even if the proper crimp tool is available. An alternative approach is to buy ready-made lengths of ribbon cable with female DuPont connectors already crimped, and cut these down to make the required cables. These are readily available on eBay, and can save a lot of work.

Note that the core colours shows in this section are for clarity only, and have no other significance.

Standard Sensor Connector Cable
The Sensor Connector Cable is integral to the standard infra-red sensor. This cable should be shortened to approximately 6cm, and a 3-pin female DuPont connector crimped to the end, wired as shown the following diagram.

Figure 10 – Internal Sensor Cable Diagram

Double check that the order of the cores in the 3-pin connector is correct. If it is not, the crimped connections can be removed from the plastic shell by carefully prising up the small black tab and sliding the connector out.

Power/Data Connector Cable
The Power/Data Connector Cable has a GX16-5 chassis plug on one end, and a 5-pin female DuPont connector on the other, wired as shown the following diagram. Note that the connections from pins 2 & 3 to the Rx & Tx connections on the Interface Board are crossed over.

Figure 11 – Internal Power/Data Cable Diagram

A suitable length of ribbon cable can be used for this cable, the required length of the cable is approximately 6cm overall.

The cable ends are soldered onto the GX16-5 chassis plugs following the wiring the diagram above. A short length of heatshrink sleeve, 2.5mm unshrunk diameter, is recommended on each core to protect the soldered connection and provide some strain relief.

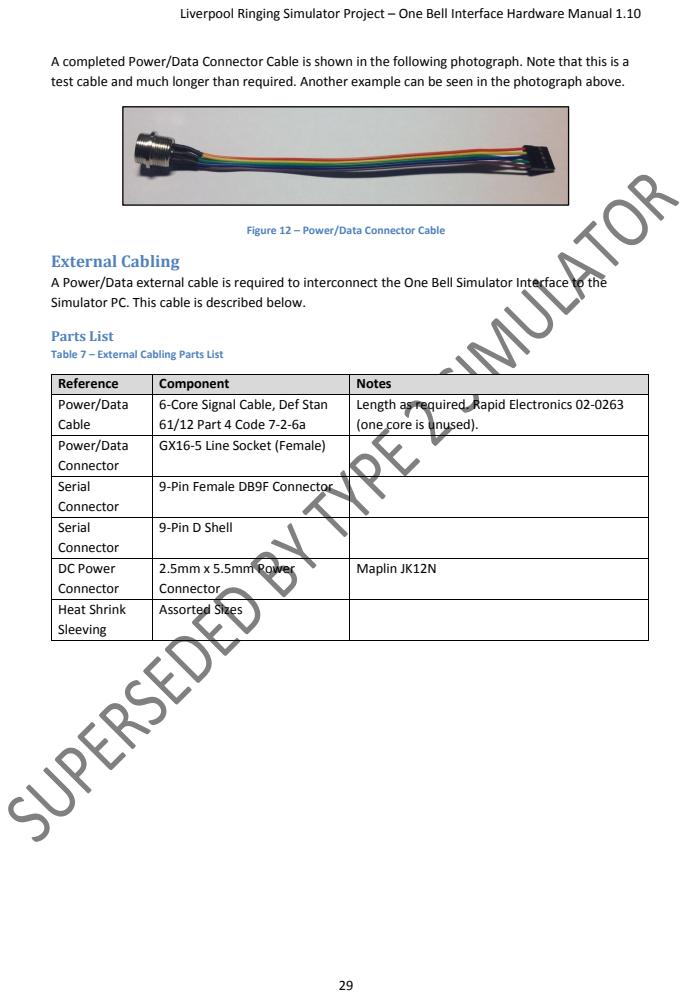
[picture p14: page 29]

A completed Power/Data Connector Cable is shown in the following photograph. Note that this is a
test cable and much longer than required. Another example can be seen in the photograph above.

Figure 12 – Power/Data Connector Cable

External Cabling
A Power/Data external cable is required to interconnect the One Bell Simulator Interface to the
Simulator PC. This cable is described below.

Parts List
Table 7 – External Cabling Parts List

Reference | Component | Notes
Power/Data Cable | 6-Core Signal Cable, Def Stan 61/12 Part 4 Code 7-2-6a | Length as required. Rapid Electronics 02-0263 (one core is unused).

Power/Data Connector | GX16-5 Line Socket (Female)

Serial Connector | 9-Pin Female DB9F Connector

Serial Connector | 9-Pin D Shell

DC Power Connector | 2.5mm x 5.5mm Power Connector | Maplin JK12N

Heat Shrink Sleeving | Assorted Sizes

Power/Data Cable
A single Power/Data Cable is required to connect the One Bell Simulator Interface to the Simulator PC, and to supply power to the Interface from a plug-in power supply. The wiring of the Simulator Data Cable is shown in the following diagram.

Figure 13 – Simulator Data Cable Wiring

The cable used is Def Stan 61/12 Part 4 Code 7-2-6a multicore cable, with one core unused. Cable lengths up to 25m have tested successfully.

The DC power connector is 2.5mm x 5.5mm, centre pin positive. The power supply cores are soldered to a pigtail of twin core cable within the D-connector cover shell, and the joints covered in heatshrink sleeving. The pigtail is then brought out through the rear cable entry and soldered to the power connector.

The core colours used in the Simulator Power/Data Cable are shown in the following table.

Table 8 – Simulator Data Cable Wiring Colours

Pin | Colour
1 | Black
2 | Yellow
3 | Green
4 | Blue
5 | Red
N/C | White

A completed test Power/Data Cable is shown in the following photograph.

Figure 14 – Power/Data Cable

Power Supply
A plug-in power supply is required to supply power to the Simulator Interface.
- A regulated DC power supply rated at 1A with multiple selectable output voltages is recommended, for example Maplin part number L82BF or equivalent.
- The output connector required is 2.5mm x 5.5mm, centre pin positive.
- The output voltage of the power supply should be adjusted so that the supply voltage at the Simulator Interface is at least 7.5 volts, measured at the cathode (striped) end of D1, with the Sensor connected.
- The supply voltage may be higher than that required to maintain 7.5 volts at the Interface, but this may result in overheating of the voltage regulator IC1 if the input voltage is excessive.
- As a guideline, a supply voltage of 9V has been found sufficient to maintain the required voltage with a 25m Power/Data cable.

### Firmware Upload

The firmware for the One Bell Simulator Interface Board is released under the GNU General Public Licence (GPL), Version 3, and the source code and other supporting files can be downloaded from GitHub.

- https://github.com/Simulators/simulator/tree/master/firmware/onebellinterface

The One Bell Simulator Interface firmware is held in non-volatile flash memory on the ATtiny85 microcontroller. It should only be necessary to re-upload the software in the event that the microcontroller is replaced, the flash memory has become corrupted, or the Simulator Interface firmware requires updating.

The firmware code needs to be uploaded to the microcontroller on the One Bell Simulator Interface PCB. Although the software development environment (described in the Software Manual) is based on the Arduino platform, the One Bell Simulator Interface does not use the Arduino bootloader, and it is not possible to upload the firmware over the interface’s RS-232 serial port. Firmware is uploaded using a hardware programmer via the ICSP header pins provided on the interface PCB.

There are two main options for the hardware programmer:

- A dedicated hardware ISP programmer such as the AVR ISP²³
- An Arduino add-on board or shield such as the Arduino ISP²⁴ or the BoardStuff UNO Multi Programming Shield²⁵
- An Arduino board (with one additional component) used as an ISP programmer.

The last of these requires no special hardware, and is the approach described in this document. There are also many tutorials online, including on the Arduino website²⁶

23 http://www.atmel.com/tools/avrispmkii.aspx 24 http://www.arduino.cc/en/Main/ArduinoISP 25 http://www.boardstuff.co.uk/
26 http://www.arduino.cc/en/Tutorial/ArduinoISP

Preparing the Environment
Perform the following steps to prepare the PC software environment for compiling and uploading the One Bell Simulator Interface firmware:
- Download and install the latest Arduino IDE package²⁷. At the time of writing this was

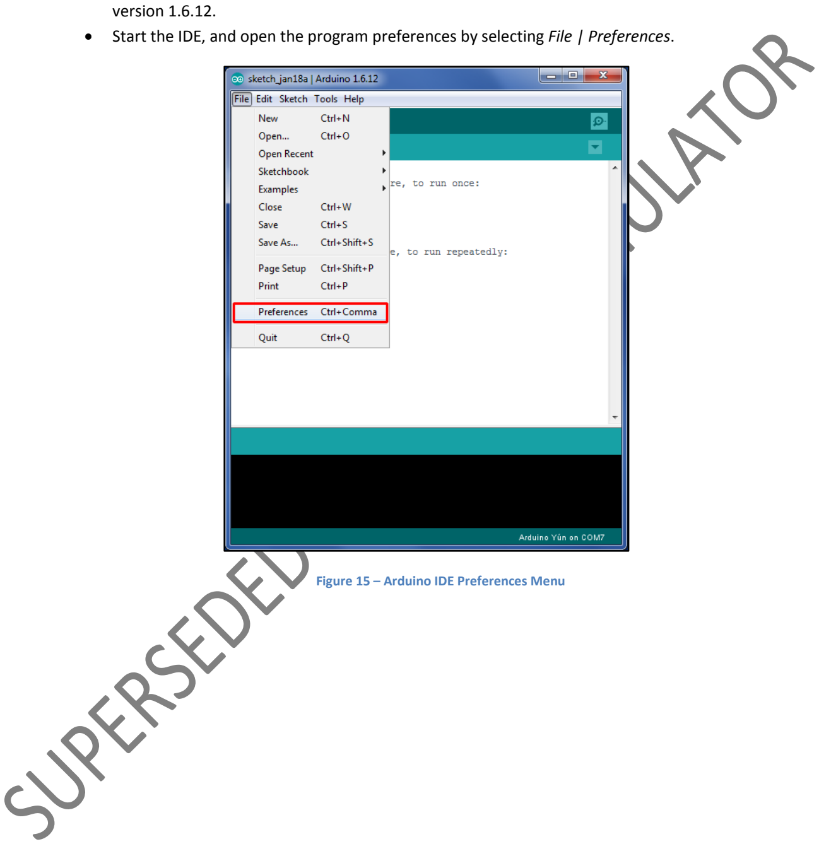
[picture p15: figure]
version 1.6.12.

- Start the IDE, and open the program preferences by selecting File | Preferences.

Figure 15 – Arduino IDE Preferences Menu

27 http://www.arduino.cc/en/Main/Software

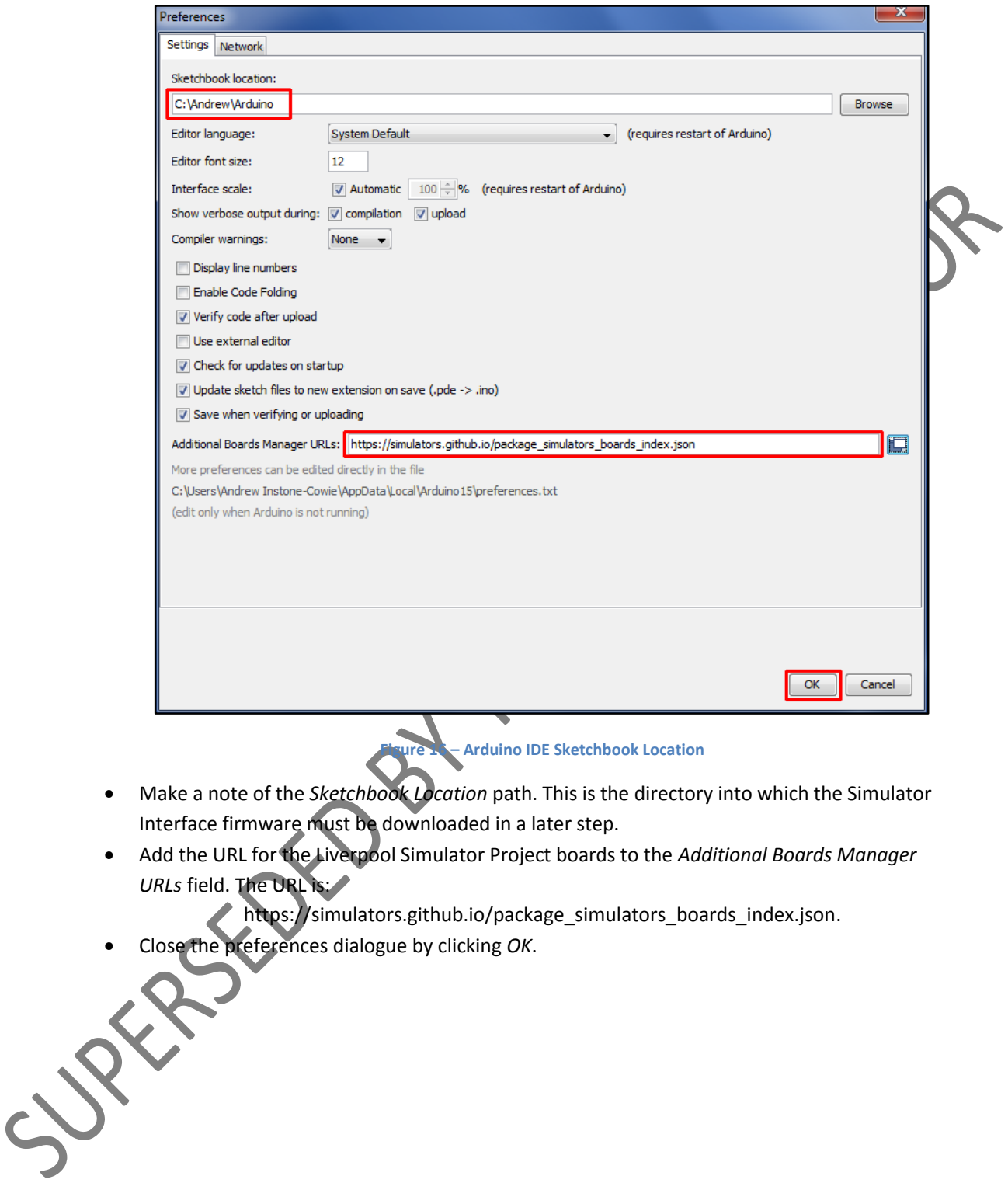
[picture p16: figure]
URLs field. The URL is: https://simulators.github.io/package_simulators_boards_index.json.

Figure 16 – Arduino IDE Sketchbook Location

- Make a note of the Sketchbook Location path. This is the directory into which the Simulator Interface firmware must be downloaded in a later step.
- Add the URL for the Liverpool Simulator Project boards to the Additional Boards Manager
- Close the preferences dialogue by clicking OK.

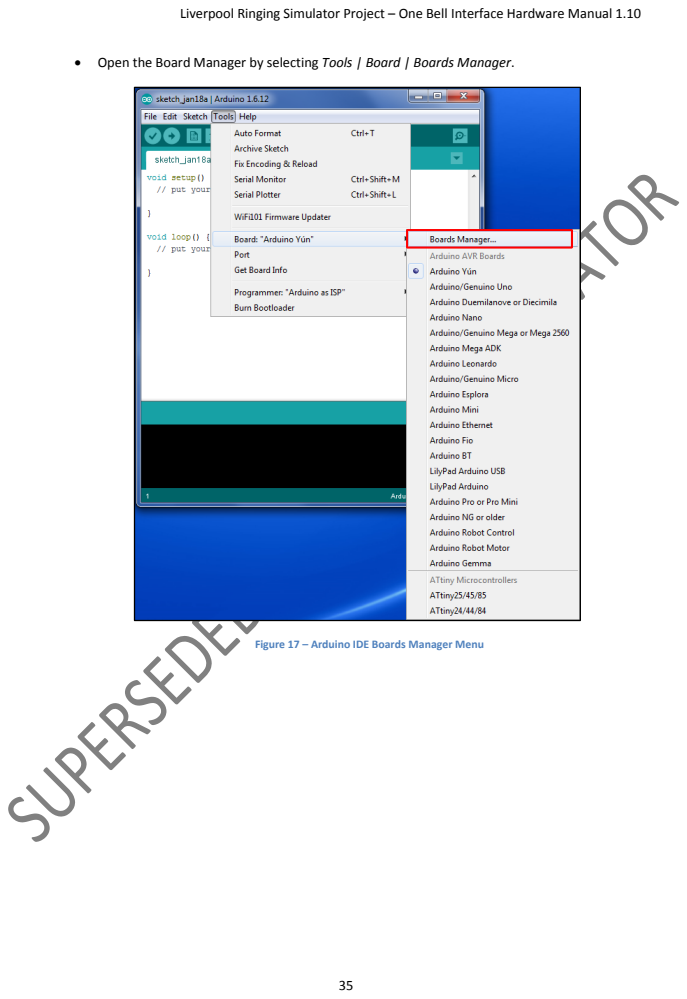
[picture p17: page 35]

• Open the Board Manager by selecting Tools | Board | Boards Manager.

Figure 17 – Arduino IDE Boards Manager Menu

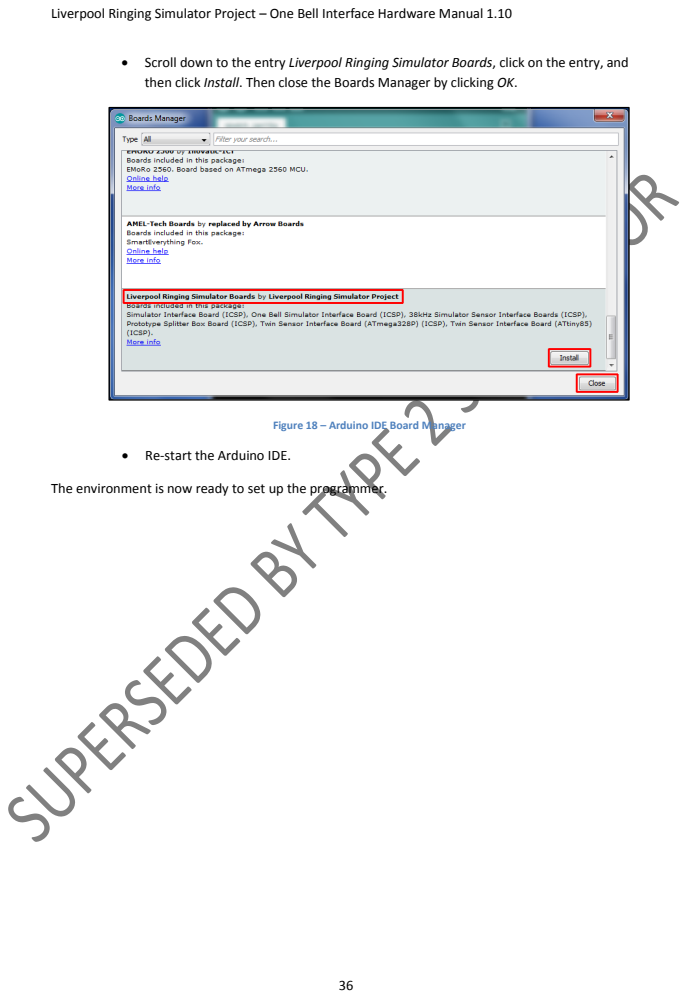
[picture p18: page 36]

• Scroll down to the entry Liverpool Ringing Simulator Boards, click on the entry, and
then click Install. Then close the Boards Manager by clicking OK.

Figure 18 – Arduino IDE Board Manager

• Re-start the Arduino IDE.

The environment is now ready to set up the programmer.

Preparing the Programmer
The programmer is an unmodified Arduino Uno board running a sketch which allows it to operate as an ISP programmer.

This requires an Arduino Uno board, and a Type A to Type B USB cable (sometimes known as a printer cable).

Figure 19 – Arduino USB Cable

The Arduino website has instructions²⁸ on connecting the Arduino board to a computer, installing drivers and setting up the IDE.

Perform the following steps to prepare the programmer Arduino Uno board:

- Connect the B end of the USB cable to the Arduino Uno board to be used as the programmer. From now on this board is referred to simply as the programmer.
- Connect the A end of the USB cable to the computer.
- Follow the instructions on the Arduino site to install drivers (if necessary), and select the correct port and board type for the programmer in the IDE.

28 http://arduino.cc/en/guide/windows

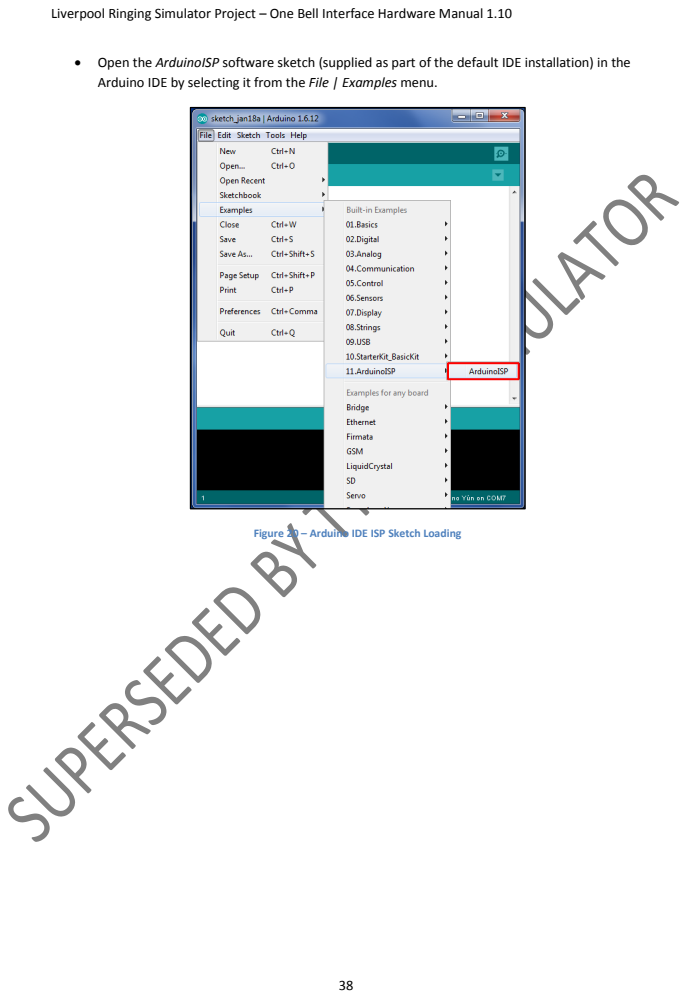
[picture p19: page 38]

• Open the ArduinoISP software sketch (supplied as part of the default IDE installation) in the
Arduino IDE by selecting it from the File | Examples menu.

Figure 20 – Arduino IDE ISP Sketch Loading

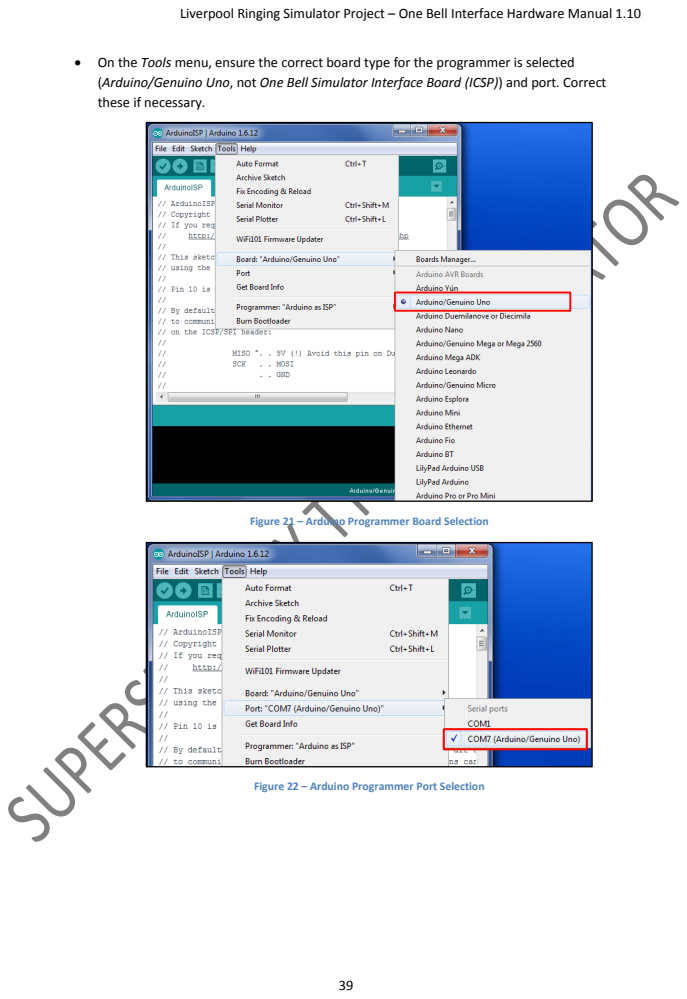
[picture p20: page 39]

• On the Tools menu, ensure the correct board type for the programmer is selected
(Arduino/Genuino Uno, not One Bell Simulator Interface Board (ICSP)) and port. Correct
these if necessary.

Figure 21 – Arduino Programmer Board Selection

Figure 22 – Arduino Programmer Port Selection

- Click the upload (arrow) button on the IDE toolbar. The ArduinoISP code will be compiled and uploaded to the programmer. Verify that the upload completed successfully by looking

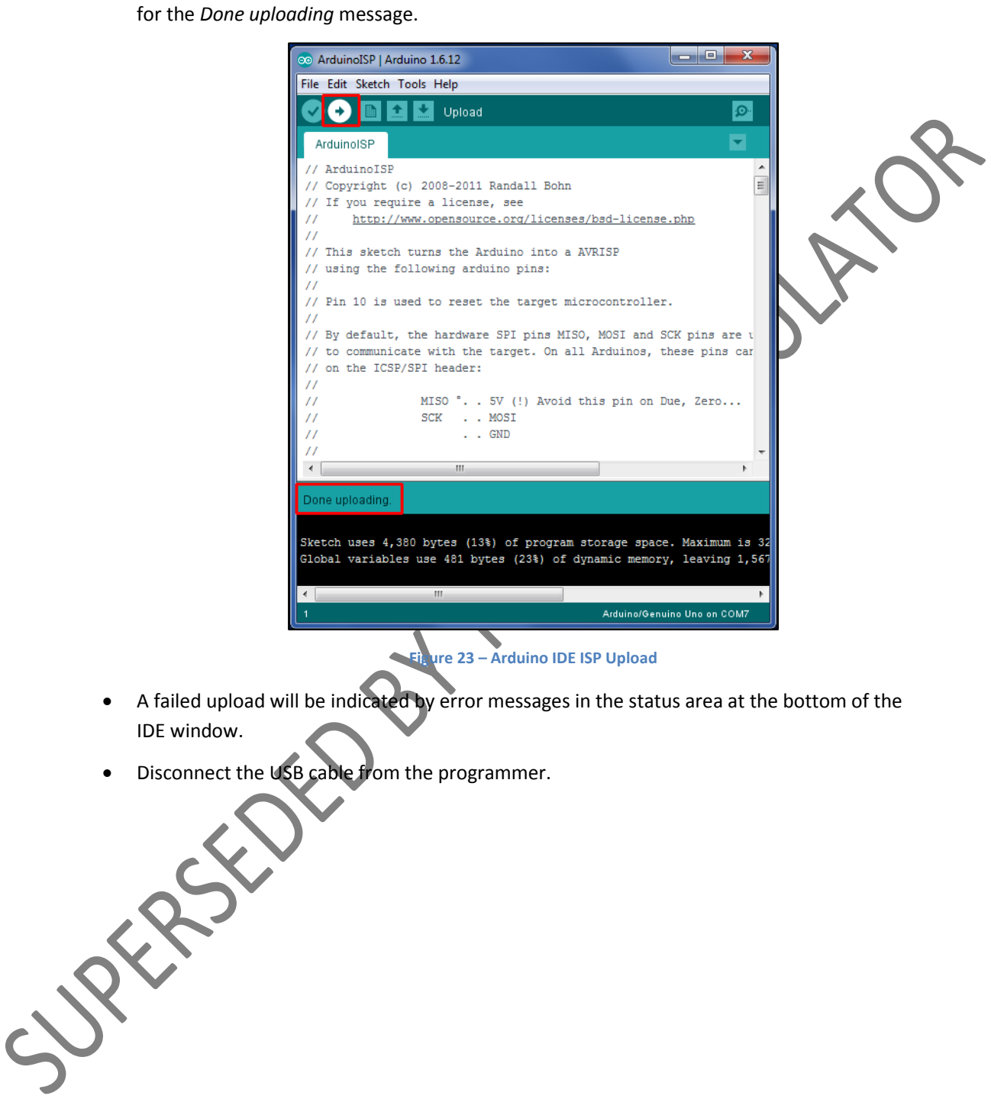
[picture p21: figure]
for the Done uploading message.; Figure 23 – Arduino IDE ISP Upload; IDE window.

- A failed upload will be indicated by error messages in the status area at the bottom of the
- Disconnect the USB cable from the programmer.

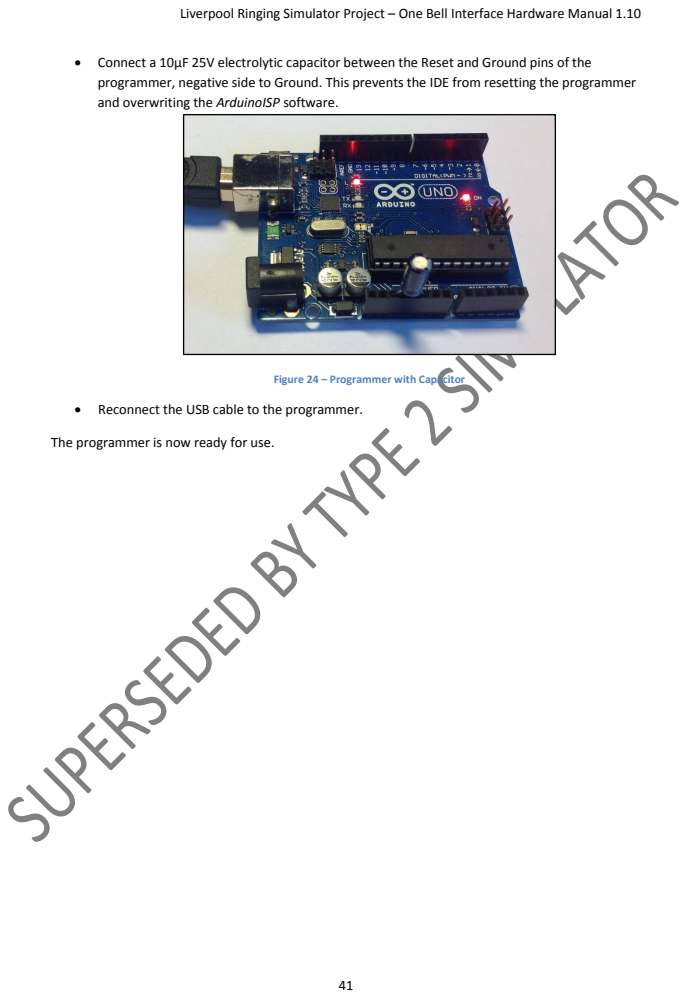
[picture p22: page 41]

• Connect a 10µF 25V electrolytic capacitor between the Reset and Ground pins of the
programmer, negative side to Ground. This prevents the IDE from resetting the programmer
and overwriting the ArduinoISP software.

Figure 24 – Programmer with Capacitor

• Reconnect the USB cable to the programmer.

The programmer is now ready for use.

Setting the Fuses
Perform the following steps to set the microcontroller fuses. The fuses and their values are explained in a previous section of this manual.
- Disconnect the USB cable from the programmer.
- Disconnect the sensor from the interface PCB.
- Connect the ICSP pins on the Simulator Interface to the ICSP pins on the programmer with jumper wires as shown in the following diagram.
- Pin 1 on the One Bell Simulator Interface PCB is top left, identified by a white stripe.
- Pin 1 on the programmer is top left. Note that pin 5 on the One Bell Simulator Interface PCB is connected to pin 10 on the programmer.

Figure 25 – Programmer Connections

- The following photograph shows the programmer connected to an interface board, including the connection to pin 10 of the programmer (orange wire), not to the ICSP pin.

Figure 26 – Programmer Connected to One Bell Simulator Interface Board

- Reconnect the USB cable to the programmer.

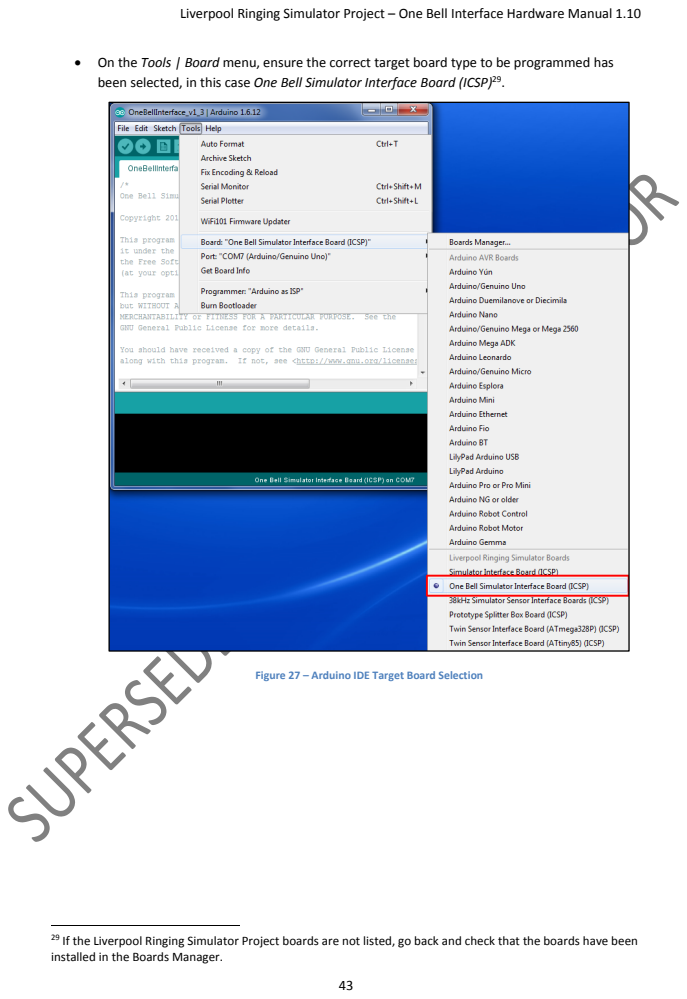
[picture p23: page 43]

• On the Tools | Board menu, ensure the correct target board type to be programmed has
been selected, in this case One Bell Simulator Interface Board (ICSP)²⁹

Figure 27 – Arduino IDE Target Board Selection

29 If the Liverpool Ringing Simulator Project boards are not listed, go back and check that the boards have been
installed in the Boards Manager.

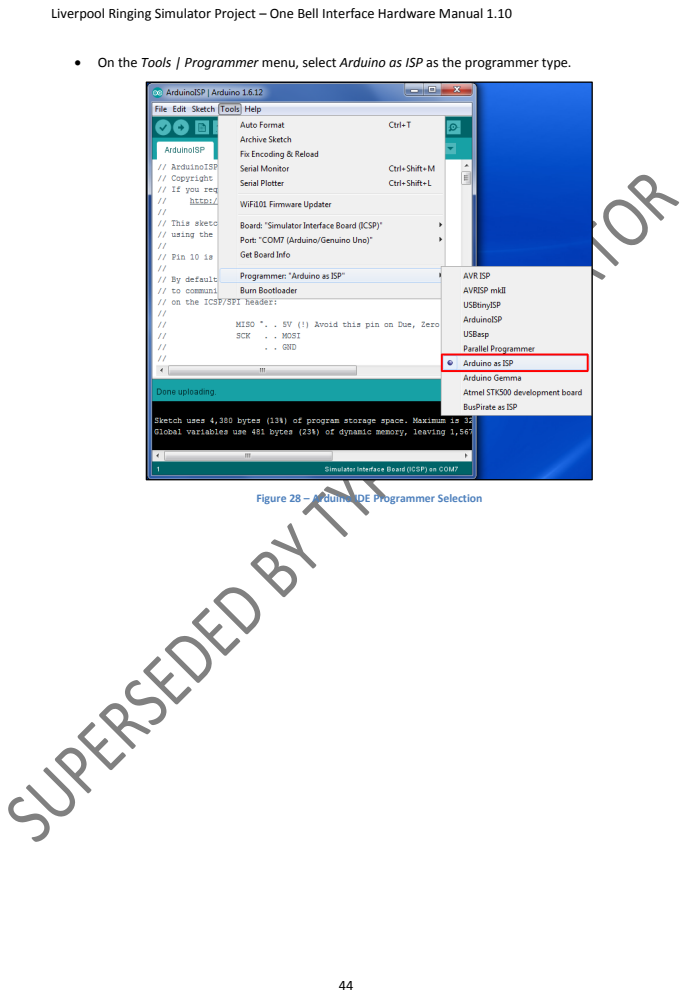
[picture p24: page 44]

• On the Tools | Programmer menu, select Arduino as ISP as the programmer type.

Figure 28 – Arduino IDE Programmer Selection

- On the Tools menu, select Burn Bootloader. The microcontroller fuses on the Simulator Interface Board will be set. Verify that the burn process completed successfully by looking for the Done burning bootloader message.

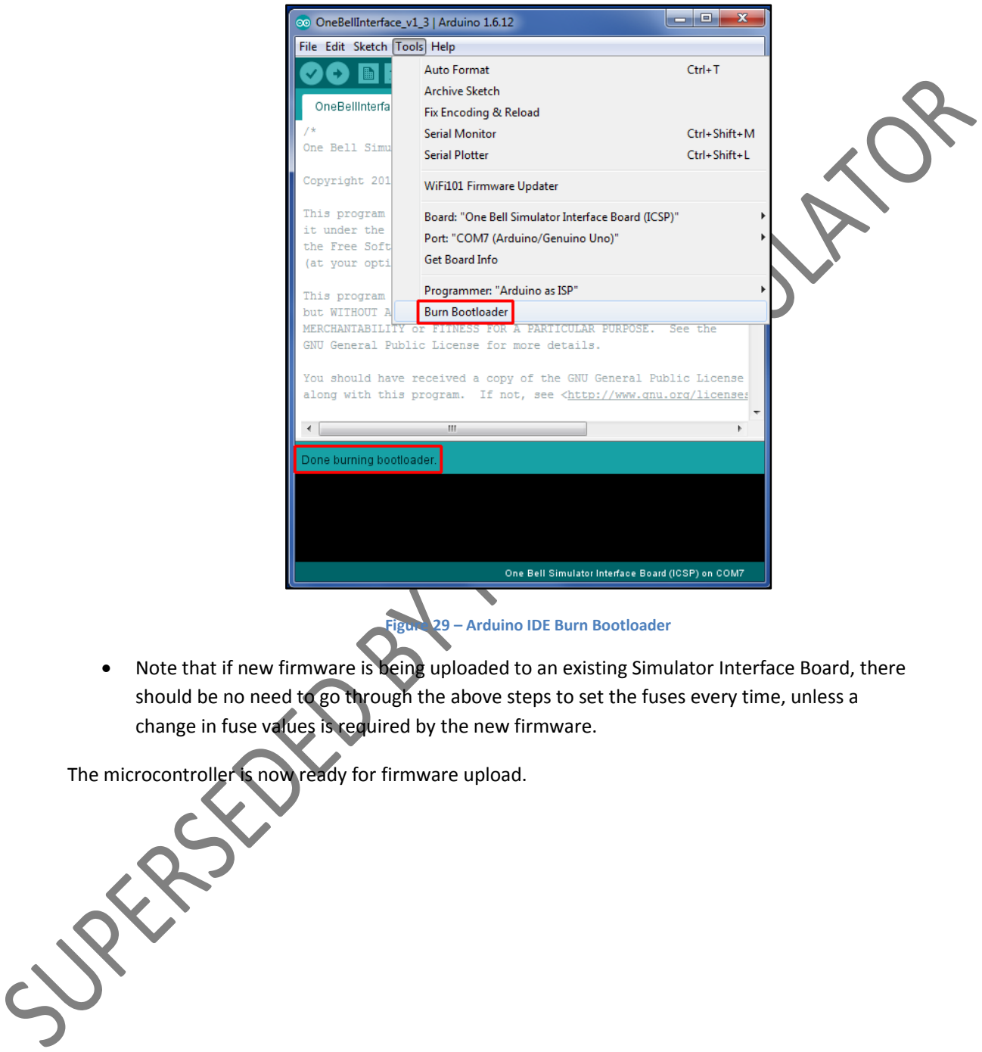
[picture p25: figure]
Figure 29 – Arduino IDE Burn Bootloader

- Note that if new firmware is being uploaded to an existing Simulator Interface Board, there should be no need to go through the above steps to set the fuses every time, unless a change in fuse values is required by the new firmware.

The microcontroller is now ready for firmware upload.

Firmware Upload
Perform the following steps to upload the One Bell Simulator Interface firmware to the board.
- Connect the One Bell Simulator Interface Board to the programmer as described in the previous section.
- Download the One Bell Simulator Interface firmware and unpack the files into the Arduino IDE sketchbook directory noted earlier. Note that all the firmware files must be unpacked into the directory; it is not possible to compile the firmware code from within a downloaded zip file.
- Load the firmware into the Arduino IDE by double clicking the name of the main file, e.g. OneBellInterface_v1_3.ino.
- On the Tools | Board menu, as above ensure that the correct board type to be programmed
has been selected, in this case One Bell Simulator Interface Board (ICSP).
- On the Tools | Programmer menu, as above select Arduino as ISP as the programmer type.
- Click the upload (arrow) button on the IDE toolbar. The Simulator Interface firmware will be compiled and uploaded to the interface board. Verify that the upload completed successfully by looking for the Done uploading message.

Figure 30 – Arduino IDE Firmware Upload

- A failed upload will be indicated by error messages in the status area at the bottom of the IDE window.
- When the upload has completed the One Bell Simulator Interface board will be reset, and on restarting the red diagnostic LED will flash according to the firmware version, for example one long and three short flashes indicates firmware version 1.3.
- Disconnect the USB cable from the programmer.

- Disconnect the programmer from the One Bell Simulator Interface Board.
- Note that when uploading new firmware to an existing One Bell Simulator Interface Board, the Sensor and the Power/Data Cable must be disconnected from the One Bell Simulator Interface.

The Simulator Interface board now has the firmware installed, and is ready for final assembly.

### Interface Assembly

Final assembly of the components is as follows.

- Fit the Power/Data Connector Cable assembly to the end of the enclosure and tighten the securing nut.
- Connect all the cables to their respective pins on the One Bell Simulator Interface Board, and carefully fit the lid to the enclosure using the screws supplied.

An example of a completed One Bell Simulator Interface is shown in the following photograph.

Figure 31 – Completed One Bell Simulator Interface

### Installation

### Simulator Interface

The One Bell Simulator Interface is located in the belfry, attached to the frame in a location such that the sensor tube is perpendicular to the face of the shroud of the wheel, in the same manner as a

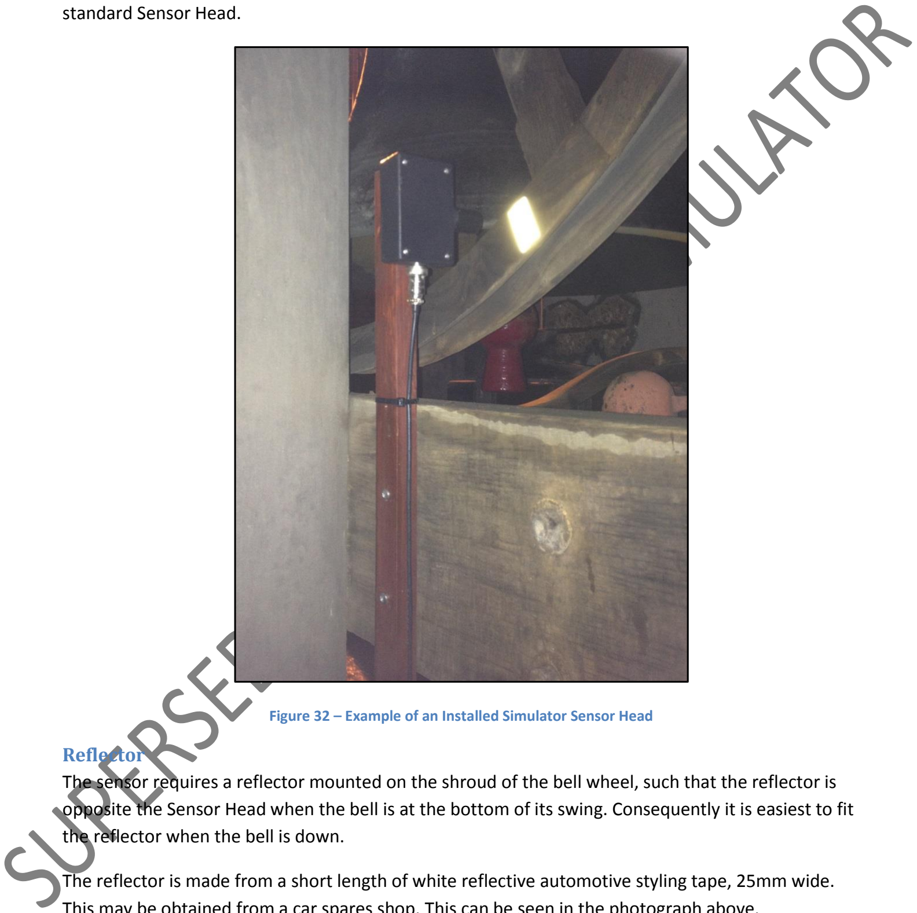
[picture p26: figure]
standard Sensor Head.; Reflector; the reflector when the bell is down.

Figure 32 – Example of an Installed Simulator Sensor Head

The sensor requires a reflector mounted on the shroud of the bell wheel, such that the reflector is opposite the Sensor Head when the bell is at the bottom of its swing. Consequently it is easiest to fit

The reflector is made from a short length of white reflective automotive styling tape, 25mm wide. This may be obtained from a car spares shop. This can be seen in the photograph above.

Calibration
As supplied, the infra-red detector sensor modules were found to draw approximately 55 – 60mA, much more than the specified 25mA, and were excessively sensitive. The small calibration screw on the end of the module may be used to reduce both the current consumption and sensitivity of the detector.

A useful starting point for sensitivity adjustment has been found to be to reduce the sensitivity of the sensor such that it does not trigger when placed perpendicular to a piece of grey card at a distance of 90mm. The multi-turn adjustment screw is turned anti-clockwise until the indicator LED on the back of the module just goes out. This gives an effective trigger distance with the reflective tape of about 300mm. This also reduces the supply current to approximately 21mA untriggered, 28mA triggered, although this is variable between modules.

The sensor should then be adjusted in the belfry for optimum sensitivity.

### Simulator Power/Data Cable

The Simulator Power/Data Cable is routed from the One Bell Simulator Interface down to the Simulator PC.

- The cable should be secured so as to prevent the weight of the cable pulling on the connectors.
- The minimum diameter of any holes along the cable route is approximately 20mm, to pass the locking ring on the GX16-5 connector which is approximately 18mm in diameter.
- Alternatively, if it is practicable to solder connectors in-situ, a minimum hole diameter of approximately 6mm is adequate for the suggested cable type.

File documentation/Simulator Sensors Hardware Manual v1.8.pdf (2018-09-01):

# The Liverpool Ringing Simulator

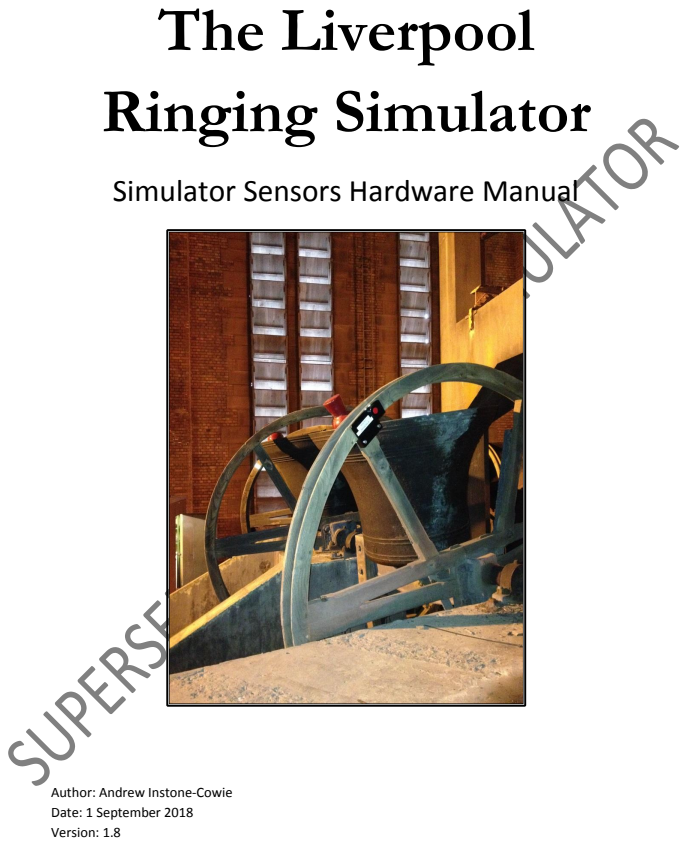
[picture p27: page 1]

Simulator Sensors Hardware Manual

Author: Andrew Instone-Cowie
Date: 1 September 2018
Version: 1.8

### Contents

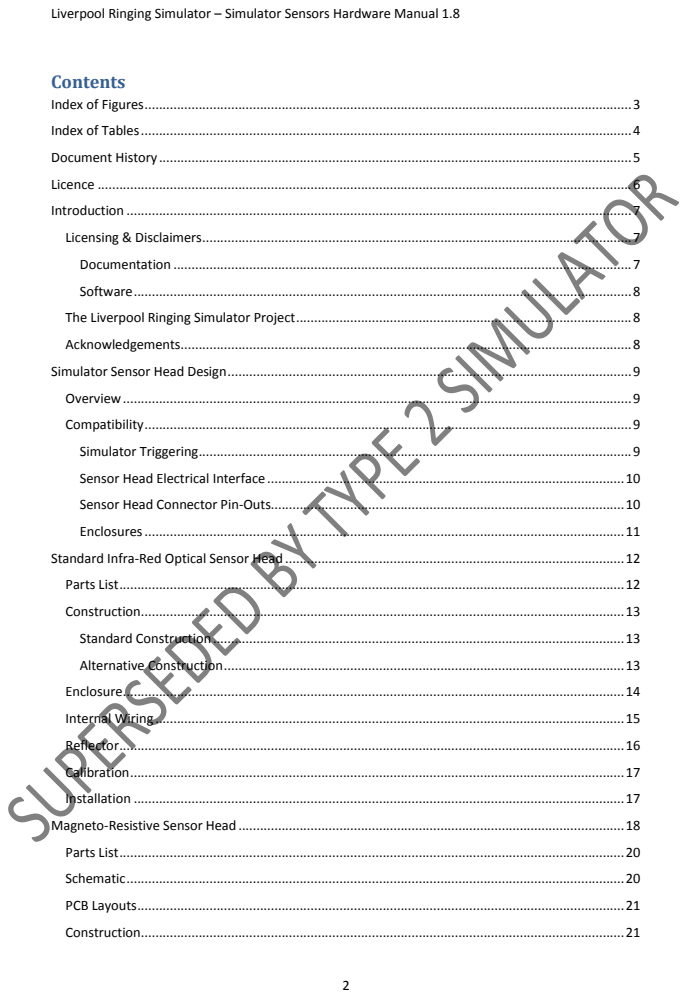
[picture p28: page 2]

Liverpool Ringing Simulator – Simulator Sensors Hardware Manual 1.8

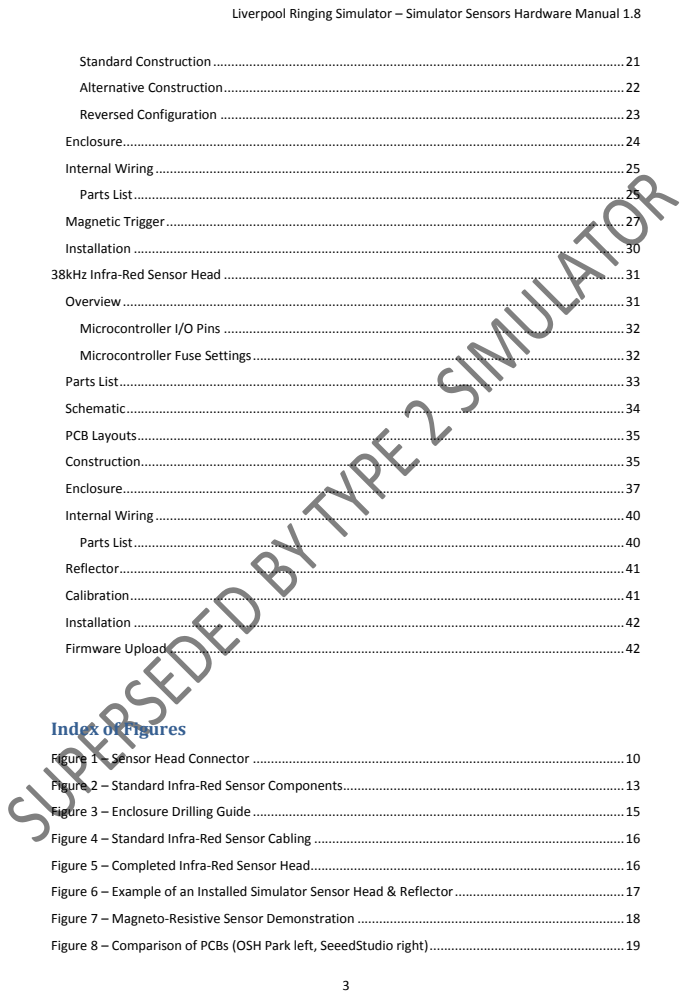
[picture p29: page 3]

Standard Construction..................................................................................................................21
Alternative Construction...............................................................................................................22
Reversed Configuration ................................................................................................................23
Enclosure...........................................................................................................................................24
Internal Wiring ..................................................................................................................................25
Parts List........................................................................................................................................25
Magnetic Trigger...............................................................................................................................27
Installation ........................................................................................................................................30
38kHz Infra-Red Sensor Head ...............................................................................................................31
Overview...........................................................................................................................................31
Microcontroller I/O Pins ...............................................................................................................32
Microcontroller Fuse Settings.......................................................................................................32
Parts List............................................................................................................................................33
Schematic..........................................................................................................................................34
PCB Layouts.......................................................................................................................................35
Construction......................................................................................................................................35
Enclosure...........................................................................................................................................37
Internal Wiring ..................................................................................................................................40
Parts List........................................................................................................................................40
Reflector............................................................................................................................................41
Calibration.........................................................................................................................................41
Installation ........................................................................................................................................42
Firmware Upload ..............................................................................................................................42

Index of Figures

Figure 1 – Sensor Head Connector .......................................................................................................10
Figure 2 – Standard Infra-Red Sensor Components..............................................................................13
Figure 3 – Enclosure Drilling Guide .......................................................................................................15
Figure 4 – Standard Infra-Red Sensor Cabling ......................................................................................16
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

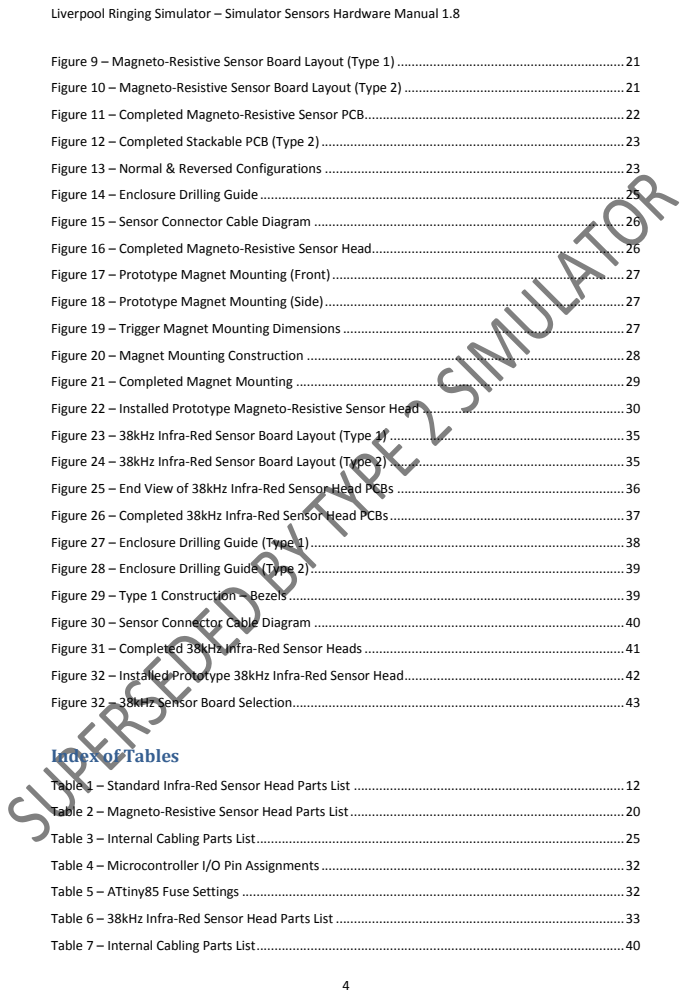
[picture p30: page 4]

Figure 9 – Magneto-Resistive Sensor Board Layout (Type 1) ...............................................................21
Figure 10 – Magneto-Resistive Sensor Board Layout (Type 2) .............................................................21
Figure 11 – Completed Magneto-Resistive Sensor PCB........................................................................22
Figure 12 – Completed Stackable PCB (Type 2)....................................................................................23
Figure 13 – Normal & Reversed Configurations ...................................................................................23
Figure 14 – Enclosure Drilling Guide.....................................................................................................25
Figure 15 – Sensor Connector Cable Diagram ......................................................................................26
Figure 16 – Completed Magneto-Resistive Sensor Head......................................................................26
Figure 17 – Prototype Magnet Mounting (Front).................................................................................27
Figure 18 – Prototype Magnet Mounting (Side)...................................................................................27
Figure 19 – Trigger Magnet Mounting Dimensions..............................................................................27
Figure 20 – Magnet Mounting Construction ........................................................................................28
Figure 21 – Completed Magnet Mounting ...........................................................................................29
Figure 22 – Installed Prototype Magneto-Resistive Sensor Head ........................................................30
Figure 23 – 38kHz Infra-Red Sensor Board Layout (Type 1) .................................................................35
Figure 24 – 38kHz Infra-Red Sensor Board Layout (Type 2) .................................................................35
Figure 25 – End View of 38kHz Infra-Red Sensor Head PCBs ...............................................................36
Figure 26 – Completed 38kHz Infra-Red Sensor Head PCBs.................................................................37
Figure 27 – Enclosure Drilling Guide (Type 1).......................................................................................38
Figure 28 – Enclosure Drilling Guide (Type 2).......................................................................................39
Figure 29 – Type 1 Construction – Bezels.............................................................................................39
Figure 30 – Sensor Connector Cable Diagram ......................................................................................40
Figure 31 – Completed 38kHz Infra-Red Sensor Heads........................................................................41
Figure 32 – Installed Prototype 38kHz Infra-Red Sensor Head.............................................................42
Figure 32 – 38kHz Sensor Board Selection............................................................................................43

Index of Tables

Table 1 – Standard Infra-Red Sensor Head Parts List ...........................................................................12
Table 2 – Magneto-Resistive Sensor Head Parts List............................................................................20
Table 3 – Internal Cabling Parts List......................................................................................................25
Table 4 – Microcontroller I/O Pin Assignments....................................................................................32
Table 5 – ATtiny85 Fuse Settings..........................................................................................................32
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

### Document History

Version | Author | Date | Changes
1.0 | A J Instone-Cowie | 09/08/2015 | First Issue
1.1 | A J Instone-Cowie | 15/08/2015 | Added photo of Rev C magneto-resistive sensor PCB.
1.2 | A J Instone-Cowie | 30/10/2015 | Revised ATtiny85 fuse settings.
1.3 | A J Instone-Cowie | 10/02/2016 | Clarified construction and component details.
1.4 | A J Instone-Cowie | 13/04/2016 | Added details of magnet mountings.
1.5 | A J Instone-Cowie | 12/05/2016 | Added reference to SeeedStudio as an alternative PCB manufacturer. Added further details to magneto-resistive sensors.
1.6 | A J Instone-Cowie | 17/08/2016 | Minor design change: Replace SA5.0CA bi-directional TVS diodes with SA5.0A uni-directional component. Change description of non-stackable/stackable magento-resistive sensors to “Type 1” & “Type 2”.
1.7 | A J Instone-Cowie | 17/01/2017 | Minor updates.
1.8 | A J Instone-Cowie | 01/09/2018 | Watermark added: Superseded by Type 2 Simulator.

Copyright ©2015-18 Andrew Instone-Cowie.

Cover photograph: Rare earth magnet trigger for prototype magneto-resistive sensor, Liverpool Cathedral.

### Licence

This work is licensed under a Creative Commons Attribution-ShareAlike 4.0 International License.¹

Unless otherwise separately undertaken by the Licensor, to the extent possible, the Licensor offers the Licensed Material as-is and as-available, and makes no representations or warranties of any kind concerning the Licensed Material, whether express, implied, statutory, or other. This includes, without limitation, warranties of title, merchantability, fitness for a particular purpose, non-infringement, absence of latent or other defects, accuracy, or the presence or absence of errors, whether or not known or discoverable. Where disclaimers of warranties are not allowed in full or in part, this disclaimer may not apply to You.

To the extent possible, in no event will the Licensor be liable to You on any legal theory (including, without limitation, negligence) or otherwise for any direct, special, indirect, incidental, consequential, punitive, exemplary, or other losses, costs, expenses, or damages arising out of this Public License or use of the Licensed Material, even if the Licensor has been advised of the possibility of such losses, costs, expenses, or damages. Where a limitation of liability is not allowed in full or in part, this limitation may not apply to You.

1 http://creativecommons.org/licenses/by-sa/4.0/

### Introduction

This Hardware Manual describes the design and construction of Sensor Heads for a ringing simulator interface which allows a sensor or sensors, attached to one or more real tower bells or teaching dumb bells, to be connected to a computer simulator package such as Abel²

, Beltower³ or Virtual
Belfry⁴
, via a Simulator Interface.
- Parts lists and schematics are provided. Links are also provided to suggested sources of parts, including ready-made printed circuit boards.
- Links are provided to the associated firmware source code, PCB CAD files and other supporting data hosted on GitHub.
- This is a build-it-yourself project. No pre-built hardware is available.

Design and construction details for the Simulator Interface itself are covered separately in an accompanying Hardware and Software Manuals.

### Licensing & Disclaimers

Documentation
All original manuals and other documentation (including PCB layout CAD files and schematics) released as part of the Liverpool Ringing Simulator project⁵ are released under the Creative Commons Attribution-ShareAlike 4.0 International License (CC BY-SA),⁶ which includes the following disclaimers:

Unless otherwise separately undertaken by the Licensor, to the extent possible, the Licensor offers the Licensed Material as-is and as-available, and makes no representations or warranties of any kind concerning the Licensed Material, whether express, implied, statutory, or other. This includes, without limitation, warranties of title, merchantability, fitness for a particular purpose, non-infringement, absence of latent or other defects, accuracy, or the presence or absence of errors, whether or not known or discoverable. Where disclaimers of warranties are not allowed in full or in part, this disclaimer may not apply to You.

To the extent possible, in no event will the Licensor be liable to You on any legal theory (including, without limitation, negligence) or otherwise for any direct, special, indirect, incidental, consequential, punitive, exemplary, or other losses, costs, expenses, or damages arising out of this Public License or use of the Licensed Material, even if the Licensor has been advised of the possibility of such losses, costs, expenses, or damages. Where a limitation of liability is not allowed in full or in part, this limitation may not apply to You.

2 http://www.abelsim.co.uk/3 http://www.beltower.co.uk/
4 http://www.belfryware.com/
5 http://www.simulators.org.uk
6 http://creativecommons.org/licenses/by-sa/4.0/

Software
All original software released as part of the Liverpool Ringing Simulator project is released under the GNU General Public Licence (GPL), Version 3⁷
, and carries the following disclaimers:

This program is free software: you can redistribute it and/or modify it under the terms of the GNU General Public License as published by the Free Software Foundation, either version 3 of the License, or (at your option) any later version.

This program is distributed in the hope that it will be useful, but WITHOUT ANY WARRANTY; without even the implied warranty of MERCHANTABILITY or FITNESS FOR A PARTICULAR PURPOSE. See the GNU General Public License for more details.

### The Liverpool Ringing Simulator Project

The use of simulators has great potential in the training of new ringers, and therefore the Liverpool Ringing Simulator Project seeks to promote the installation and take-up of simulators as a teaching aid in other towers. The project presents the work undertaken at the Cathedral, and other towers, and makes it freely available for ringers to build and install simulators at relatively low cost.

The project is based on work undertaken at Liverpool Cathedral to provide a 12-bell simulator for demonstration and training purposes. For more details of the background to the project, please refer to the main Simulator Interface Hardware or Software Manuals.

### Acknowledgements

The Liverpool Ringing Simulator project relies extensively on work already undertaken by others, notably David Bagley (developer of the Bagley MBI), Chris Hughes and Simon Feather (developers of the Abel simulator software package), Derek Ballard (developer of the Beltower simulator software package), Doug Nichols (developer of the Virtual Belfry simulator software package), and others. Their invaluable contributions are hereby acknowledged. Sources used are referenced in the footnotes throughout.

Thanks are also owed to the Ringing Masters of Liverpool Cathedral and of St George’s, Isle of Man, for their willingness to be the crash test dummies of simulator design and testing.

7 http://www.gnu.org/licenses/gpl-3.0.en.html

### Simulator Sensor Head Design

### Overview

This manual contains the details of three separate Sensor Head designs:

- A Sensor Head adopted as the project standard by the Liverpool Ringing Simulator Project, based on a commercially available modulated infra-red detector unit, marketed as an “obstacle sensor” for educational robotics projects. These sensors are available quite inexpensively, and the Sensor Heads are very straightforward to construct.
- A magneto-resistive Sensor Head, based closely on a design⁸ by Aidan Hedley, using a Honeywell magneto-resistive sensor IC⁹
, activated by a small, powerful rare earth magnet. This sensor has no moving or optical parts, and is completely free of optical interference. It also draws much less current than an optical sensor. A variation of this sensor is also suitable for integration into the One Bell Simulator Interface.
- An experimental, proof-of-concept infra-red Sensor Head using a 38kHz infra-red receiver. This Sensor Head design is aimed mainly at experimenters and prototype builders, and is not expected to be widely deployed.

Note: All the Sensor Heads described in this Hardware Manual are designed for connection via a Simulator Interface. They are not suitable for direct connection to a Simulator PC.

### Compatibility

Simulator Triggering
There are generally two approaches used by Simulators when detecting signals from Sensor Heads:
- The twin trigger approach uses two triggers (for example, optical reflectors) on the shroud of the wheel of each bell, one of which triggers at the moment that the bell would strike at handstroke, the other at the moment that the bell would strike at backstroke. The Simulator triggers the simulated sound of the bell as soon as the signal pulse is received (triggered by the reflector travelling past the sensor as the bell is on its way up to the balance), and then ignores the next signal pulse (as the first reflector travels back past the sensor as the bell is on its way down), and so on.
- The second approach is to use a single trigger, which triggers as the bell passes through the bottom dead centre of its swing. A delay is then applied (either in the Simulator Interface or the Simulator Software Package) before the Simulator triggers the simulated sound of the bell. This approach is simpler to implement, and the single trigger is much easier to align accurately against the Sensor Head with the bell down. Work by John Norris¹⁰ has shown that this approach can provide an acceptable degree of accuracy, with any errors considered too small to be detectable to the human ear.

8 http://www.gremlyn.plus.com/ahme/mag_sen.html
9 http://sensing.honeywell.com/product-page?pr_id=36114 10 http://www.jrnorris.co.uk/strike.html

The Liverpool Ringing Simulator project’s Simulator Interfaces adopt the single trigger approach, on the grounds of simplicity of installation and compatibility with other similar systems. More details of the design of a Simulator using this approach can be found in the accompanying Software Manual.

The Sensor Heads described in this Hardware Manual are intended for use with a single trigger system, although they could in principle be adapted to a twin trigger approach. Such adaptation is beyond the scope of this manual.

Sensor Head Electrical Interface
The Sensor Heads operate on a 5V DC power supply, and the output is at 5V logic levels.
- The output of the Sensor Head is inverted; in the normal untriggered state the output is held at +5V (logic HIGH), when triggered the output drops close to 0V (logic LOW) for the duration of the detected pulse.
- Pulse duration is typically in the range 5ms – 20ms, depending on Sensor Head type and installation factors.
- The Sensor Heads are not suitable for direct operation at RS-232 voltages.

Sensor Head Connector Pin-Outs
All Sensor Heads developed across the Liverpool Ringing Simulator Project use the same GX16-4 (also known as “aviation”) connectors for the cabling connection to the Simulator Interface. These are of the same type and are wired following the same convention as other sensors, with an extension for dual-headed Sensor Heads.

The wiring of the male chassis plug connector is illustrated in the following diagram:

Figure 1 – Sensor Head Connector

In some installations cabling may be simplified by mounting two detectors in a single sensor head, for example where the Sensor Head is mounted between two adjacent wheels (examples of this approach are shown elsewhere in this manual). Pin 4 of the GX16-4 connector may optionally be used for the input from a second detector, with the appropriate modifications to the corresponding Sensor Interface connector.

Enclosures
The project standard Sensor Head enclosure is the WCAH 2855 black ABS box manufactured by Wisher Enterprise Co Ltd.
- This enclosure can be obtained from Maplin, ESR Components and Velleman, and measures 85mm x 55mm x 30mm (external) overall.
- Use of a standard enclosure simplifies PCB design, and allows different Sensor Heads to be

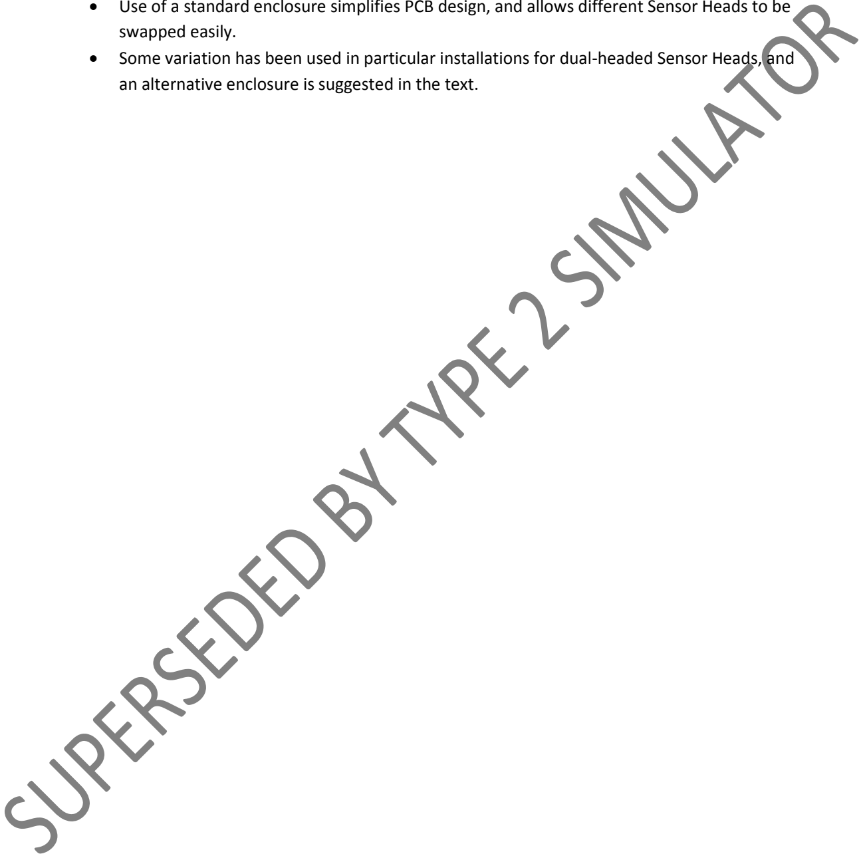
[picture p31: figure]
swapped easily.

- Some variation has been used in particular installations for dual-headed Sensor Heads, and an alternative enclosure is suggested in the text.

### Standard Infra-Red Optical Sensor Head

The Sensor Heads adopted as the project standard by the Liverpool Ringing Simulator Project are based on a commercially available modulated infra-red detector unit, marketed as an “obstacle sensor” for educational robotics projects. These sensors are available pre-assembled and relatively inexpensively, and consequently the Sensor Heads are very straightforward to construct.

The sensor emits and detects infra-red light modulated at high frequency. This makes the sensor much less sensitive than visible light or unmodulated infra-red sensors to interference from ambient lighting conditions.

The specification¹¹,12 of the detectors is as follows:

- Model: E18-D80NK
- Output current: DC / 100mA / 5V supply
- Current consumption: DC <25mA
- Response time: <2ms
- Angle: more than 15°,
- Effective distance: Adjustable from 3-80CM
- Working environment temperature: -25 °C ~ 55 °C

The actual current drawn by the detectors was found to be approximately 28mA in the triggered state, and 21mA in the untriggered state, after calibration for simulator use as described below.

The sense wire current was measured at approximately 130μA trigged, 0μA untriggered. The output is inverted, that is normally high (nominally +5V) when untriggered, dropping low (nominally 0V) when triggered.

The sensor and signal connector are mounted in a standard plastic enclosure.

### Parts List

Table 1 – Standard Infra-Red Sensor Head Parts List

Component | Notes
WCAH 2855 ABS Black Enclosure | ESR Components 400-595, Maplin BZ72P, Velleman WCAH2855
No2 x 9mm Stainless Steel Self Tapping Screws | eBay
30mm x 20mm (Diameter) Black Plastic Conduit
GX16-4 Chassis Plug (Male) | Signal Connector
SA5.0A | Transient voltage suppression (TVS) diode
E18-D80NK Infra-Red Sensor | eBay

11 http://hobbycomponents.com/sensors/213-ir-infrared-obstacle-avoidance-sensor-e18-d80nk 12 http://www.61mcu.com/?product-56.html

The components (excluding the TVS diode) of one standard infra-red Sensor Head are shown in the following photograph:

Figure 2 – Standard Infra-Red Sensor Components

### Construction

Standard Construction
The infra-red sensor is mounted through the side of the enclosure using the plastic nuts supplied with the sensor. These should be tightened finger-tight only; do not use tools.

Once the sensor is installed, lightly file or sand the exposed threads so that the masking tube is a firm tight push fit on the end of the sensor.

The GX16-4 connector is mounted through the end of the enclosure. As shown the drilling diagram below, it is necessary to remove the plastic PCB ribs from this end of the enclosure to accommodate the connector.

Alternative Construction
As noted above, in some installations cabling in the belfry may be simplified by mounting two detectors in a single Sensor Head, for example where the Sensor Head is mounted between two adjacent wheels. In this case the second sensor signal connection makes use of the spare pin of the GX16-4 connector, with the appropriate modifications to the corresponding Sensor Interface connector.

Two alternative versions are illustrated below. The example on the left is housed in the standard WCAH 2855 enclosure, the offset version in a larger Hammond 1591XXBBK ABS Enclosure, 113mm x 63mm x 31mm.

### Enclosure

The suggested enclosure for the standard infra-red Sensor Head is the project standard WCAH 2855 black ABS box manufactured by Wisher Enterprise Co Ltd.

- This enclosure can be obtained from Maplin, ESR Components and Velleman, and is the same enclosure adopted as a standard for Sensor Heads across the Liverpool Ringing Simulator Project.
- The enclosure is 85mm x 55mm x 30mm (external) overall.
- Drilling large diameter holes with twist drills can result in bit grabbing and damage to the enclosure. Small diameter (16mm/18mm) hole saws are available at relatively low cost (e.g. on eBay), and these make the process of drilling the enclosure much easier and safer.
- Using a sharp chisel, carefully and gently remove the PCB ribs from the inside of the enclosure as indicated on the diagram below, to allow the Power/Data connector to be mounted. Using too much force may crack the case.

- It is recommended that the lid retaining screws supplied with the enclosure are replaced with stainless steel equivalents.
- The 4.5mm mounting hole is optional. Other mounting arrangements may be devised.

The following diagram shows the suggested drilling layout for the enclosure.

Figure 3 – Enclosure Drilling Guide

### Internal Wiring

The wiring of the standard infra-red optical Sensor Head is very straightforward:

- The three-core sensor cable is integral to the infra-red sensor. This cable should be shortened to approximately 6cm, and soldered directly to the GX16-4 chassis plug following the pin-out shown above.
- Note that the sensor wires must be passed through the connector hole in the enclosure before being soldered; the sensor will not pass through the connector hole, and vice-versa.
- The SA5.0A TVS diode is soldered directly across the power supply pins in the connector. The cathode, indicated by a white stripe, must be connected to pin 1 of the GX16-4 connector¹³ .

13 Note that prior to version 1.6 of this manual, the TVS diode was a non-polarised component.

The wiring of the standard infra-red Sensor Head is illustrated in the following diagram.

Figure 4 – Standard Infra-Red Sensor Cabling

The following picture shows one completed Sensor Head, with its cover removed. (The TVS diode has not yet been fitted to this prototype unit.)

Figure 5 – Completed Infra-Red Sensor Head

### Reflector

The sensor requires a reflector mounted on the shroud of the bell wheel, such that the reflector is opposite the Sensor Head when the bell is at the bottom of its swing. Consequently the reflector should be fitted when the bell is down.

The reflector is made from a short length of white reflective automotive styling tape, 25mm wide. This may be obtained from a car spares shop. This can be seen in the installation photograph below.

### Calibration

As supplied, most of the infra-red detector sensor modules were found to draw approximately 55 – 60mA, much more than the specified 25mA, and were excessively sensitive. The small calibration screw on the end of the module may be used to reduce both the current consumption and sensitivity of the detector.

A useful starting point for sensitivity adjustment has been found to be to reduce the sensitivity of the sensor such that it does not trigger when placed perpendicular to a piece of grey card at a distance of 90mm from the end of the detector. The multi-turn adjustment screw is turned anti-clockwise until the indicator LED on the back of the module just goes out. This gives an effective maximum trigger distance with the reflective tape of about 300mm. This also reduces the supply current to approximately 21mA untriggered, 28mA triggered, although this is variable between modules.

The sensor should then be adjusted in the belfry for optimum sensitivity.

### Installation

The Sensor Head is located in the belfry, attached to the frame in a location such that the sensor tube is perpendicular to the face of the shroud of the wheel, in the same manner as a standard Sensor Head. The reflector is positioned directly opposite the Sensor Head when the bell is down.

Figure 6 – Example of an Installed Simulator Sensor Head & Reflector

### Magneto-Resistive Sensor Head

The magneto-resistive Sensor Head, which is based closely on a design¹⁴ by Aidan Hedley, uses a Honeywell magneto-resistive sensor IC¹⁵, activated by a small, powerful rare earth magnet mounted on the wheel shroud. This sensor has no moving or optical parts, and is completely free of optical interference. It also draws much less current than an optical sensor, prototypes were measured at approximately 8mA including a signal LED.

Using a magnet of the type suggested below, the maximum operating distance of the prototype was approximately 60mm (face of magnet to face of enclosure). In practice an operating distance of approximately 40mm should be reliably feasible, and this distance has been used successfully in a test installation of a sensor at Liverpool Cathedral, and on the Cathedral 6-bell Saxilby Simulator.

Figure 7 – Magneto-Resistive Sensor Demonstration

The sensor PCB contains all the components of the sensor, including the magneto-resistive sensor itself, an optional diagnostic LED, and associated components. The sensor and signal connector are mounted in the same project standard plastic enclosure as the other sensors described in this manual.

Eagle CAD and Gerber files for the board can be downloaded from GitHub. Gerber files are provided for two possible board manufacturers, OSH Park in the USA and SeeedStudio in China. There are two versions of the PCB, as is explained further in the Construction section below.

- https://github.com/Simulators/simulator/tree/master/hardware/magneticsensor
- https://oshpark.com/shared_projects/IJhg1jxK (Type 1)
- https://oshpark.com/shared_projects/AfsFCwFR (Type 2)
- http://www.seeedstudio.com

Both manufacturers have been found to supply boards of a high quality, although the Chinese boards are of a slightly lower specification (e.g. HASL finish rather than ENIG) but are considerably cheaper in quantity.

14 http://www.gremlyn.plus.com/ahme/mag_sen.html
15 http://sensing.honeywell.com/product-page?pr_id=36114

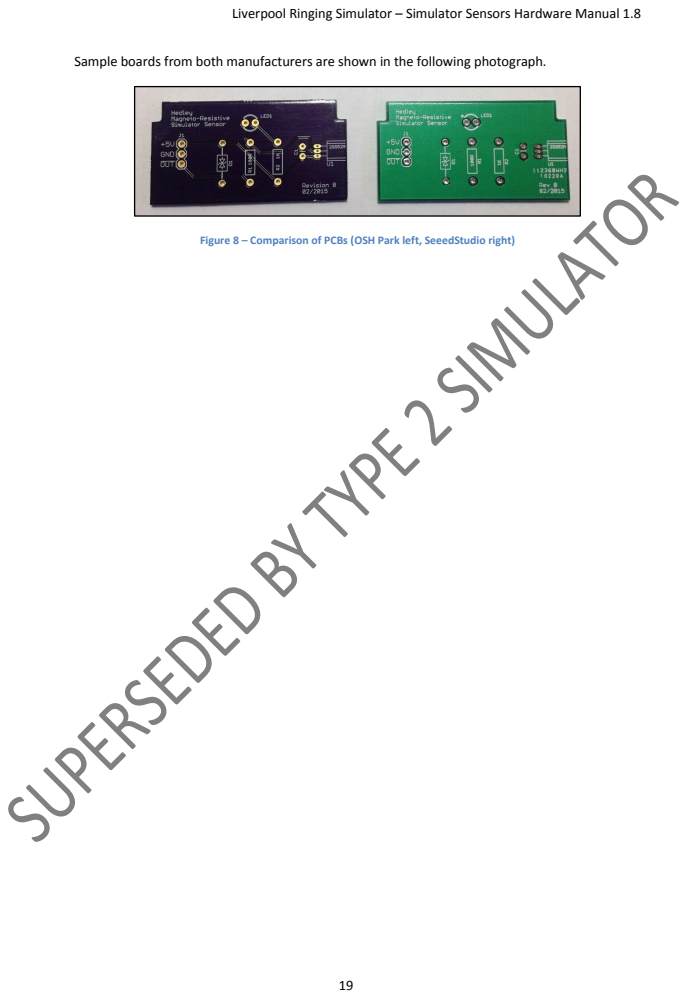
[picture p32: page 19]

Sample boards from both manufacturers are shown in the following photograph.

Figure 8 – Comparison of PCBs (OSH Park left, SeeedStudio right)

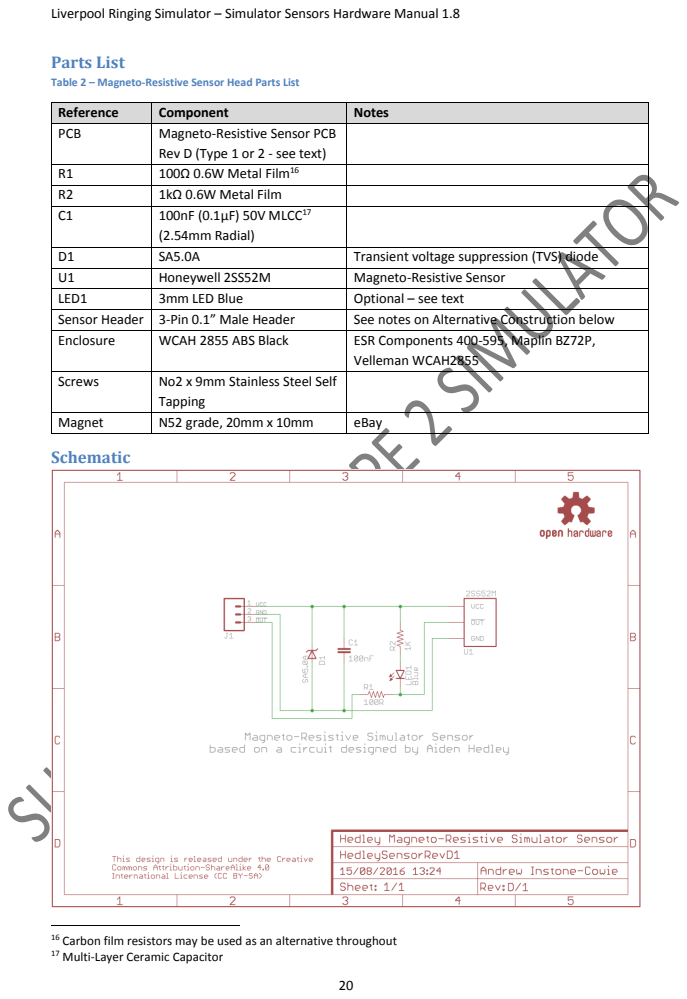
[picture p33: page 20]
Parts List; Schematic

Table 2 – Magneto-Resistive Sensor Head Parts List

Reference | Component | Notes
PCB | Magneto-Resistive Sensor PCB Rev D (Type 1 or 2 - see text)

R1 | 100Ω 0.6W Metal Film¹⁶
R2 | 1kΩ 0.6W Metal Film
C1 | 100nF (0.1µF) 50V MLCC¹⁷ (2.54mm Radial)

D1 | SA5.0A | Transient voltage suppression (TVS) diode
U1 | Honeywell 2SS52M | Magneto-Resistive Sensor
LED1 | 3mm LED Blue | Optional – see text
Sensor Header | 3-Pin 0.1” Male Header | See notes on Alternative Construction below
Enclosure | WCAH 2855 ABS Black | ESR Components 400-595, Maplin BZ72P, Velleman WCAH2855

Screws | No2 x 9mm Stainless Steel Self Tapping

Magnet | N52 grade, 20mm x 10mm | eBay

16 Carbon film resistors may be used as an alternative throughout
17 Multi-Layer Ceramic Capacitor

### PCB Layouts

The following diagrams show the layout of the magneto-resistive sensor PCBs.

Figure 9 – Magneto-Resistive Sensor Board Layout (Type 1)

Figure 10 – Magneto-Resistive Sensor Board Layout (Type 2)

### Construction

Standard Construction
There are two versions of the magneto-resistive sensor board:
- Type 1 is intended for self-contained magneto-resistive Sensor Heads connected to a separate Simulator Interface, and is the version shown in the examples in this manual.
- Type 2 is designed to integrate with the One Bell Simulator Interface board in a stacked configuration, as an alternative to an infra-red optical or other detector. This is described further in the One Bell Simulator Interface Hardware Manual.

All the components on the magneto-resistive sensor board are mounted on top, silkscreen, side of the board:

- The 2SS52M magneto-resistive sensor is mounted parallel to the PCB, approximately 2mm clear of the surface, flush with the end of the board and with the chamfers facing away from the board, so that the sensor will slide into the gap between the PCB ribs of the standard enclosure. This can be seen in the photographs below, and is intended to position the sensitive end of the sensor as close as possible to the inside of the enclosure.

- Fitting the diagnostic LED is optional, but strongly recommended. The LED is polarised, and must be mounted in the correct orientation with the cathode on the left. The cathode is usually denoted by a flat on the side of the moulding and by a shorter leg.
- Pay particular attention to the correct orientation of the polarised components D1, U1 & the LED¹⁸

A completed magneto-resistive sensor PCB is shown in the following photograph. Note that this is an earlier version of the PCB.

Figure 11 – Completed Magneto-Resistive Sensor PCB

Alternative Construction
PCB Type 2 may be used to build a magneto-resistive sensor which can be used with the One Bell Simulator Interface, as an alternative to the standard infra-red sensor. This version of the PCB is designed to stack behind the One Bell Simulator Interface in the standard enclosure.

When assembling the Type 2 PCB, the following changes are required:

- The 3-pin J1 male header pins are replaced with a 3-pin female header. This is still mounted on the top, silkscreen, side of the board. This will mate with the pins located on the back of the One Bell Simulator Interface PCB.
- D1 may be omitted. The One Bell Simulator Interface PCB includes a TVS diode.
- The LED may be mounted flush with the sensor PCB, or omitted altogether. The One Bell Simulator Interface includes a diagnostic LED.

18 Note that prior to PCB Rev D, D1 was a non-polarised component.

This configuration is described in more detail in the One Bell Simulator Interface Hardware Manual. A completed Type 2 PCB is shown in the following photograph. Note that this is an earlier version of the PCB.

Figure 12 – Completed Stackable PCB (Type 2)

Reversed Configuration
In the construction shown above the sensor is on the right hand side when viewed with the lid removed and the connector at the bottom. Where belfry installation will require the sensor to be on the left hand side, the PCB may be reversed and the header pins mounted on the rear of the board. Right and left handed configurations are illustrated in the following photograph.

Figure 13 – Normal & Reversed Configurations

### Enclosure

The suggested enclosure for the magneto-resistive Sensor Head is the project standard WCAH 2855 black ABS box manufactured by Wisher Enterprise Co Ltd.

- This enclosure can be obtained from Maplin, ESR Components and Velleman, and is the same enclosure adopted as a standard for Sensor Heads across the Liverpool Ringing Simulator Project.
- The enclosure is 85mm x 55mm x 30mm (external) overall.
- Drilling large diameter holes with twist drills can result in bit grabbing and damage to the enclosure. Small diameter (16mm/18mm) hole saws are available at relatively low cost (e.g. on eBay), and these make the process of drilling the enclosure much easier and safer.
- Using a sharp chisel, carefully and gently remove the PCB ribs from the inside of the enclosure as indicated on the diagram below, to allow the Sensor and GX16-4 signal connector to be mounted. Using too much force may crack the case.
- It is recommended that the lid retaining screws supplied with the enclosure are replaced with stainless steel equivalents.
- The 4.5mm mounting hole is optional. Other mounting arrangements may be devised.
- The 3mm hole for the LED is not required if the diagnostic LED is omitted or is mounted flush with the PCB.

The following diagram shows the suggested drilling layout for the enclosure for a Sensor Head using

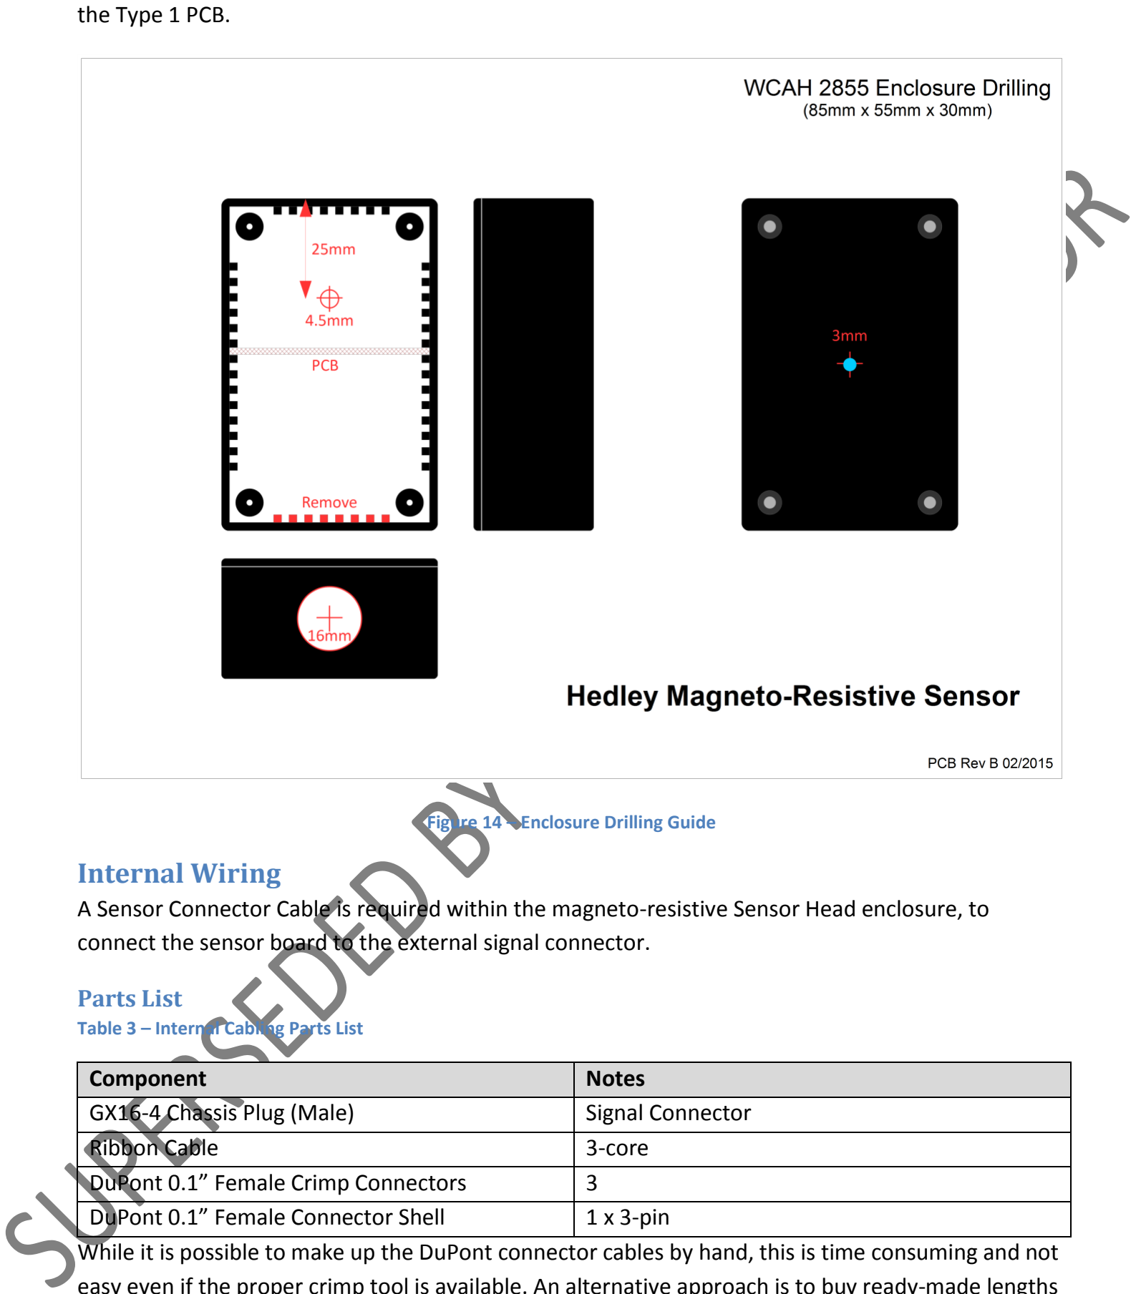
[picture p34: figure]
the Type 1 PCB.; Figure 14 – Enclosure Drilling Guide; Internal Wiring; Parts List; Table 3 – Internal Cabling Parts List; Component; Notes; GX16-4 Chassis Plug (Male); Signal Connector; Ribbon Cable; 3-core; DuPont 0.1” Female Crimp Connectors; DuPont 0.1” Female Connector Shell; 1 x 3-pin

A Sensor Connector Cable is required within the magneto-resistive Sensor Head enclosure, to connect the sensor board to the external signal connector.

While it is possible to make up the DuPont connector cables by hand, this is time consuming and not easy even if the proper crimp tool is available. An alternative approach is to buy ready-made lengths of ribbon cable with female DuPont connectors already crimped, and cut these down to make the required cables. These are readily available on eBay, and can save a lot of work.

Note that the core colours shows in this section are for clarity only, and have no other significance.

The Sensor Connector Cable has a GX16-4 chassis plug on one end, and a 3-pin female DuPont connector on the other, wired as shown the following diagram.

Figure 15 – Sensor Connector Cable Diagram

A suitable length of ribbon cable can be used for this cable, the required length is approximately 6cm overall.

The cable ends are soldered onto the GX16-4 chassis plug following the wiring the diagram above. A short length of heatshrink sleeve, 2.5mm unshrunk diameter, is recommended on each core to protect the soldered connection and provide some strain relief.

The Sensor Connector Cable can be seen in one of the following pictures, which show one completed prototype Sensor Head. The positioning of the sensor between the PCB ribs can also be seen.

Figure 16 – Completed Magneto-Resistive Sensor Head

### Magnetic Trigger

The magneto-resistive sensor is triggered by a small rare-earth magnet mounted on the shroud of the wheel, such that the magnet is opposite the centre of the Sensor Head (i.e., co-axial with the 2SS52M sensor IC) when the bell is at the bottom of its swing, similar to the alignment of a reflector and optical sensor.

The magnet used in the prototype installation is a N52 grade rare earth magnet, 20mm diameter x 10mm thick. For prototype testing a plywood cradle, illustrated below, was made which clamps around a spoke on the wheel. The magnet, here painted red, is fixed in a circular plywood mounting with epoxy adhesive.

Figure 17 – Prototype Magnet Mounting (Front) | Figure 18 – Prototype Magnet Mounting (Side)

The following less elaborate mounting is suggested for a permanent installation.

The trigger magnet is mounted in a “flange” cut from 12mm WBP plywood, which is then fixed to the shroud of the wheel using stainless steel screws or double-sided tape.

The dimensions of the mounting flange are show in the following diagram:

Figure 19 – Trigger Magnet Mounting Dimensions

The magnet mountings are constructed as follows:

- The shape of the mounting is marked out on a piece of WBP plywood, 12mm thick. A paper template may be printed out and stuck temporarily to the wood with glue or double sided tape. A suitable template is available from the GitHub repository as a PDF, and should be printed out full size with no scaling.
- The centre hole for the magnet is drilled out with a 20mm spade bit. This should be used in a bench drill press, if available, so that the hole is reasonably accurately cut and the magnet will be a close fit.
- If the mounting is to be fixed to the wheel with screws, the screw holes are also drilled. It is easier to drill all the holes before cutting the mount to size.
- The mounting is then cut and sanded to shape, and the remains of the template removed. Do not sand the inside of the central hole.

These steps are illustrated in the following series of pictures.

Figure 20 – Magnet Mounting Construction

The magnet is pushed into the central hole, and if necessary secured with a small amount of epoxy adhesive. The face of the magnet should be flush with the outer face of the mount, and note that for the Honeywell sensor the polarity of the magnet is not important.

The following picture shows a completed magnet mounting, ready for painting.

Figure 21 – Completed Magnet Mounting

Care must be taken when handling the rare earth magnets, because they are both powerful and very brittle and can strike a magnetic object with enough force to shatter the magnet. They are also susceptible to corrosion, so must be painted.

Once painted the mounting can be fixed the wheel with pan head stainless steel self-tapping screws 3.5mm in diameter and 20mm – 25mm long; the screws should not protrude through the shroud of the wheel. Alternatively the mount can be secured with double-sided tape.

### Installation

The Sensor Head is located in the belfry, attached to the frame in a location such that the magnet is positioned directly opposite the axis of the sensor IC when the bell is down. The prototype installation at Liverpool Cathedral is shown in the following photographs. (The magnet is not visible because the bell is up; the installed cradle is shown in the cover photograph of this Hardware Manual.) Note the metal offset bracket fitted to bring the magneto-resistive sensor closer to the

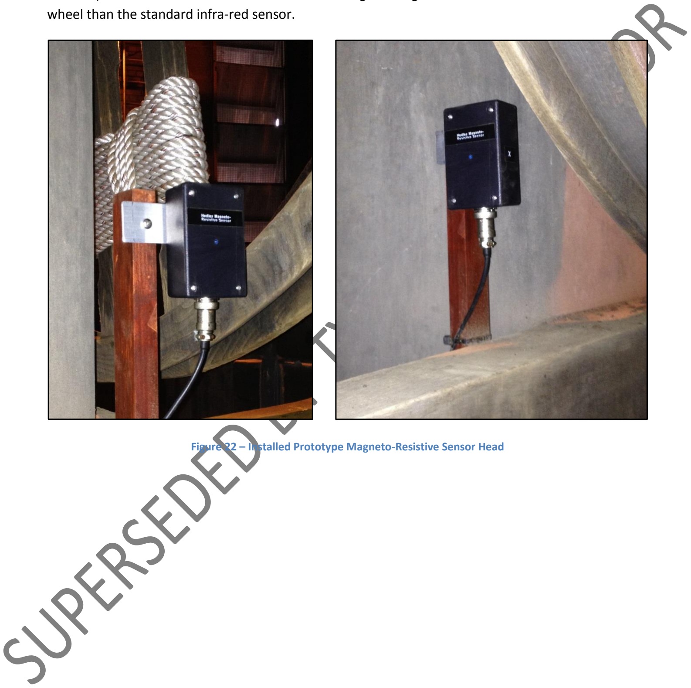
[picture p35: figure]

wheel than the standard infra-red sensor.

Figure 22 – Installed Prototype Magneto-Resistive Sensor Head

### 38kHz Infra-Red Sensor Head

### Overview

The 38kHz Infra-Red Sensor Head is an experimental, proof-of-concept sensor, using a similar approach to the commercially available modulated infra-red detector unit used in the standard infra-red sensor. This Sensor Head design is aimed mainly at experimenters and prototype builders, and is not expected to be widely deployed.

The Sensor Head uses one of the timers on an ATtiny85 microcontroller to generate a 38kHz PWM output, which drives an infra-red LED, producing a modulated infra-red output. The specification of the LED is as follows:

- Lenses Type : Crystal Clear
- Case Style : 5mm Round
- Forward Voltage : 1.5v - 1.6v
- Forward Current : 60mA
- Wavelength : 940nm
- Viewing Angle : 25deg

A fixed current limiting resistor prevents the LED from exceeding the ATtiny85 maximum current rating, and a multi-turn variable resistor allows the sensitivity to be adjusted by varying the LED current.

This infra-red light is detected using a TSSP4038 infra-red receiver¹⁹ via a reflector on the wheel. This type of sensor produces a steady output signal when a 38kHz carrier is detected²⁰. The output of the receiver is monitored by the ATtiny85, and the state of the Sensor Head output pin is set to follow changes in state in the output of the receiver.

Another microcontroller output pin sets the state of the diagnostic LED to the inverse of the IR receiver output (i.e. the LED is on when the receiver output is pulled low during a signal pulse.

The total current drawn by the prototype sensors is approximately 8.5mA untriggered, 11.5mA triggered.

Eagle CAD and Gerber files for the board can be downloaded from GitHub, and ready-made boards can be obtained from OSH Park. There are two versions of the PCB, as is explained further in the Construction section below.

- https://github.com/Simulators/simulator/tree/master/hardware/38khzsensor
- https://oshpark.com/shared_projects/t9JGGOlP (Type 1)
- https://oshpark.com/shared_projects/QSL0oWyG (Type 2)

19 http://www.vishay.com/docs/82458/tssp4038.pdf
20 Other types of 38kHz receiver only generate an output when a valid stream of modulated data is received.

Microcontroller I/O Pins
The following table shows the ATtiny85 pin assignments for the 38kHz Infra-Red Sensor Head:

Table 4 – Microcontroller I/O Pin Assignments

Arduino I/O Pin²¹ | ATtiny85 Physical Pin | Function
0 | 5 | Yellow Diagnostic LED
1 | 6 | Sensor Head Output
2 | 7 | (Spare)
3 | 2 | Infra-Red Receiver Input
4 | 3 | Infra-Red LED PWM Ouput

Microcontroller Fuse Settings
The ATtiny85 microcontroller has a number of configuration registers known as fuses. These are used to control the behaviour of the microcontroller²². Fuse values are contained in the file boards.txt described in the section on uploading firmware below, and are only written during the burn bootloader phase of programming.

Warning: Setting incorrect fuse values can render the microcontroller unusable or prevent further reprogramming without specialist hardware.

The fuse values for the 38kHz Infra-Red Sensor Head are defined in the following table.

Table 5 – ATtiny85 Fuse Settings

Fuse | Value | Notes
Low | 0xE2 | 8MHz internal oscillator, maximum clock startup delay.
High | 0XD5 | Enable serial programming, preserve EEPROM contents, Brown-out detection level 1 (2.7V).

21 Pin numbers as referenced in the Arduino programming environment.
22 Fuse tutorial (based on ATmega328P): http://www.martyncurrey.com/arduino-atmega-328p-fuse-settings/

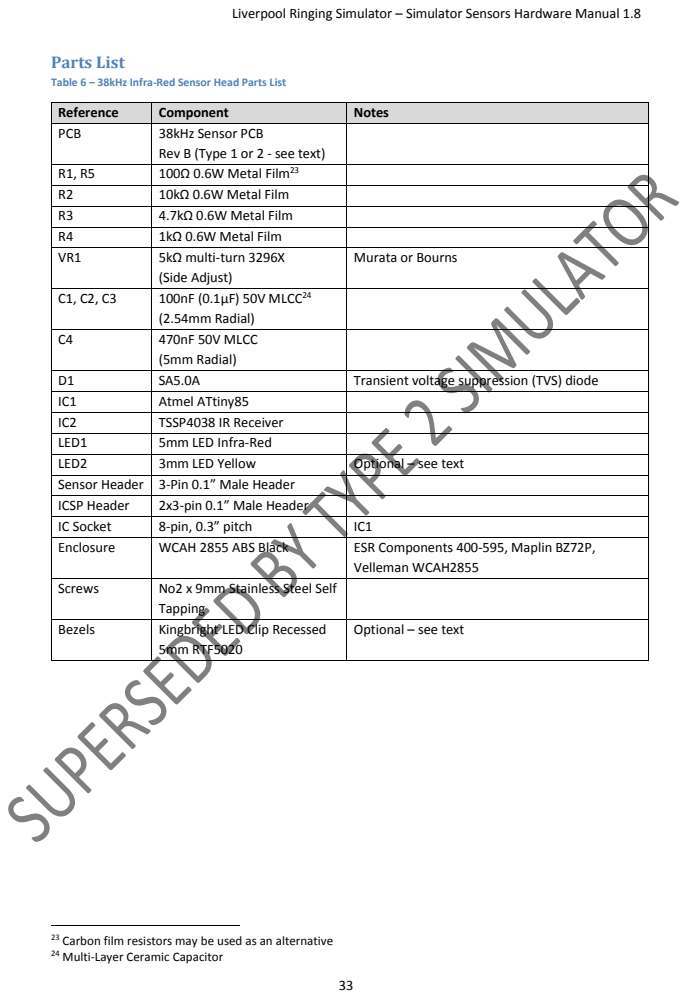
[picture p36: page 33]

Table 6 – 38kHz Infra-Red Sensor Head Parts List

Reference | Component | Notes
PCB | 38kHz Sensor PCB Rev B (Type 1 or 2 - see text)

R1, R5 | 100Ω 0.6W Metal Film²³
R2 | 10kΩ 0.6W Metal Film
R3 | 4.7kΩ 0.6W Metal Film
R4 | 1kΩ 0.6W Metal Film
VR1 | 5kΩ multi-turn 3296X (Side Adjust) | Murata or Bourns

C1, C2, C3 | 100nF (0.1µF) 50V MLCC²⁴ (2.54mm Radial)

C4 | 470nF 50V MLCC (5mm Radial)

D1 | SA5.0A | Transient voltage suppression (TVS) diode
IC1 | Atmel ATtiny85
IC2 | TSSP4038 IR Receiver
LED1 | 5mm LED Infra-Red
LED2 | 3mm LED Yellow | Optional – see text
Sensor Header | 3-Pin 0.1” Male Header
ICSP Header | 2x3-pin 0.1” Male Header
IC Socket | 8-pin, 0.3” pitch | IC1
Enclosure | WCAH 2855 ABS Black | ESR Components 400-595, Maplin BZ72P, Velleman WCAH2855

Screws | No2 x 9mm Stainless Steel Self Tapping

Bezels | Kingbright LED Clip Recessed 5mm RTF5020 | Optional – see text

23 Carbon film resistors may be used as an alternative
24 Multi-Layer Ceramic Capacitor

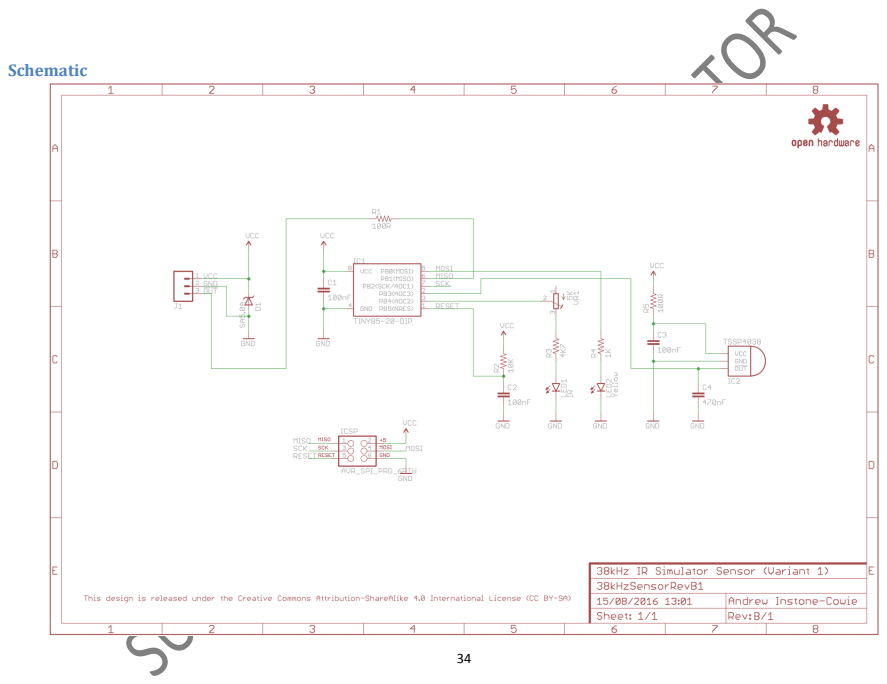
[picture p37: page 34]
Schematic

### PCB Layouts

The following diagrams show the layout of the 38kHz infra-red sensor PCBs.

Figure 23 – 38kHz Infra-Red Sensor Board Layout (Type 1)

Figure 24 – 38kHz Infra-Red Sensor Board Layout (Type 2)

### Construction

Two prototype variants of the 38kHz Infra-Red Sensor Head have been constructed. In Type 1, the IR receiver and IR LED are mounted on opposite sides of the PCB. In Type 2, they are mounted side-by-side on the top of the PCB. The objective of the Type 1 construction was to minimise the effect of side-scatter from the IR LED onto the receiver, early prototyping having suggested that this would be problematic; in practice the side-by-side Type 2 construction has been found acceptable with the body of the LED wrapped in a short length of back heatshrink sleeving.

The difference between the two board layouts can be seen in the following photographs.

Figure 25 – End View of 38kHz Infra-Red Sensor Head PCBs

All the components on the 38kHz Infra-Red Sensor Head PCB are mounted on top, silkscreen, side of the board, apart from the IR LED on the Type 1 board.

- Start by soldering the components with the lowest profile (resistors, ceramic capacitors), then the remainder of the components in order of increasing height, ending with the variable resistor and header pins.
- The use of an IC socket for IC1 is optional, but strongly recommended.
- Fitting the diagnostic LED is optional, but strongly recommended.
- The LEDs are polarised, and must be mounted in the correct orientation. The cathode is usually denoted by a flat on the side of the moulding and by a shorter leg.
- Pay particular attention to the correct orientation of the polarised components D1, IC1, IC2 & the LEDs²⁵
- Before fitting the socketed IC, connect the board to a power supply and check that +5V and 0V appear on the correct pins of the socket and on the correct header pins. Disconnect the power supply and fit the IC, observing that the polarisation dot/notch is at the bottom.
- If the board is powered up at this point, there will be no indication from the diagnostic LED. This is normal if the firmware has not yet been uploaded to the microcontroller.

25 Note that prior to PCB Rev B, D1 was a non-polarised component.

Completed 38kHz infra-red sensor PCBs of each type are shown in the following photographs. Note that these are earlier versions of the PCB.

Figure 26 – Completed 38kHz Infra-Red Sensor Head PCBs

### Enclosure

The suggested enclosure for both variants of the 38kHz infra-red Sensor Head is the project standard WCAH 2855 black ABS box manufactured by Wisher Enterprise Co Ltd.

- This enclosure can be obtained from Maplin, ESR Components and Velleman, and is the same enclosure adopted as a standard for Sensor Heads across the Liverpool Ringing Simulator Project.
- The enclosure is 85mm x 55mm x 30mm (external) overall.
- Drilling large diameter holes with twist drills can result in bit grabbing and damage to the enclosure. Small diameter (16mm/18mm) hole saws are available at relatively low cost (e.g. on eBay), and these make the process of drilling the enclosure much easier and safer.
- Using a sharp chisel, carefully and gently remove the PCB ribs from the inside of the enclosure as indicated on the diagram below, to allow the Sensor and Power/Data connector to be mounted. Using too much force may crack the case.
- It is recommended that the lid retaining screws supplied with the enclosure are replaced with stainless steel equivalents.
- The 4.5mm mounting hole is optional. Other mounting arrangements may be devised.
- The 3mm hole for the LED is not required if the diagnostic LED is omitted or is mounted flush with the PCB.

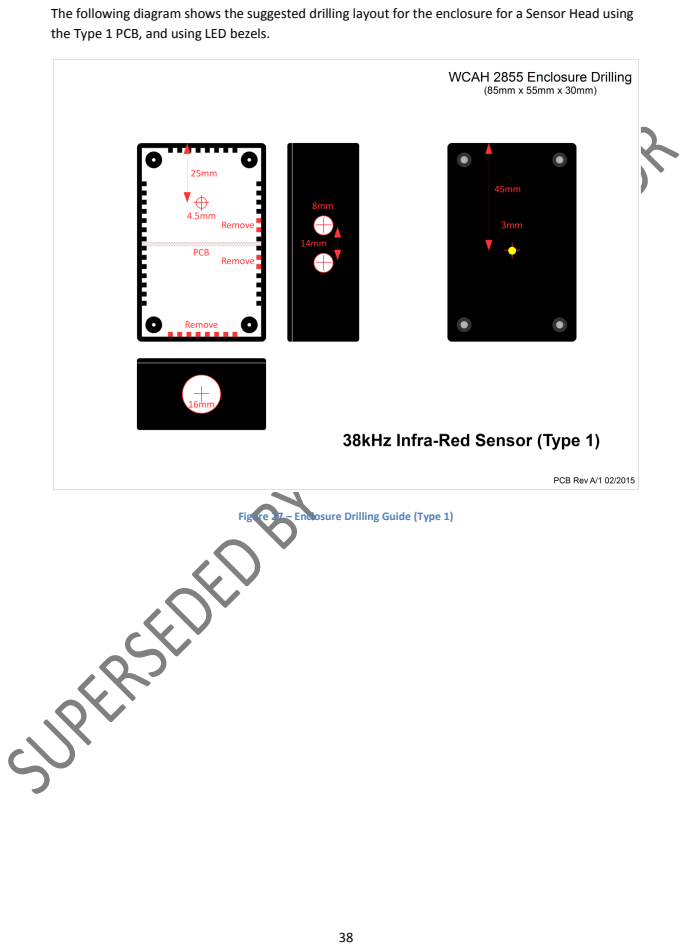
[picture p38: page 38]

The following diagram shows the suggested drilling layout for the enclosure for a Sensor Head using
the Type 1 PCB, and using LED bezels.

Figure 27 – Enclosure Drilling Guide (Type 1)

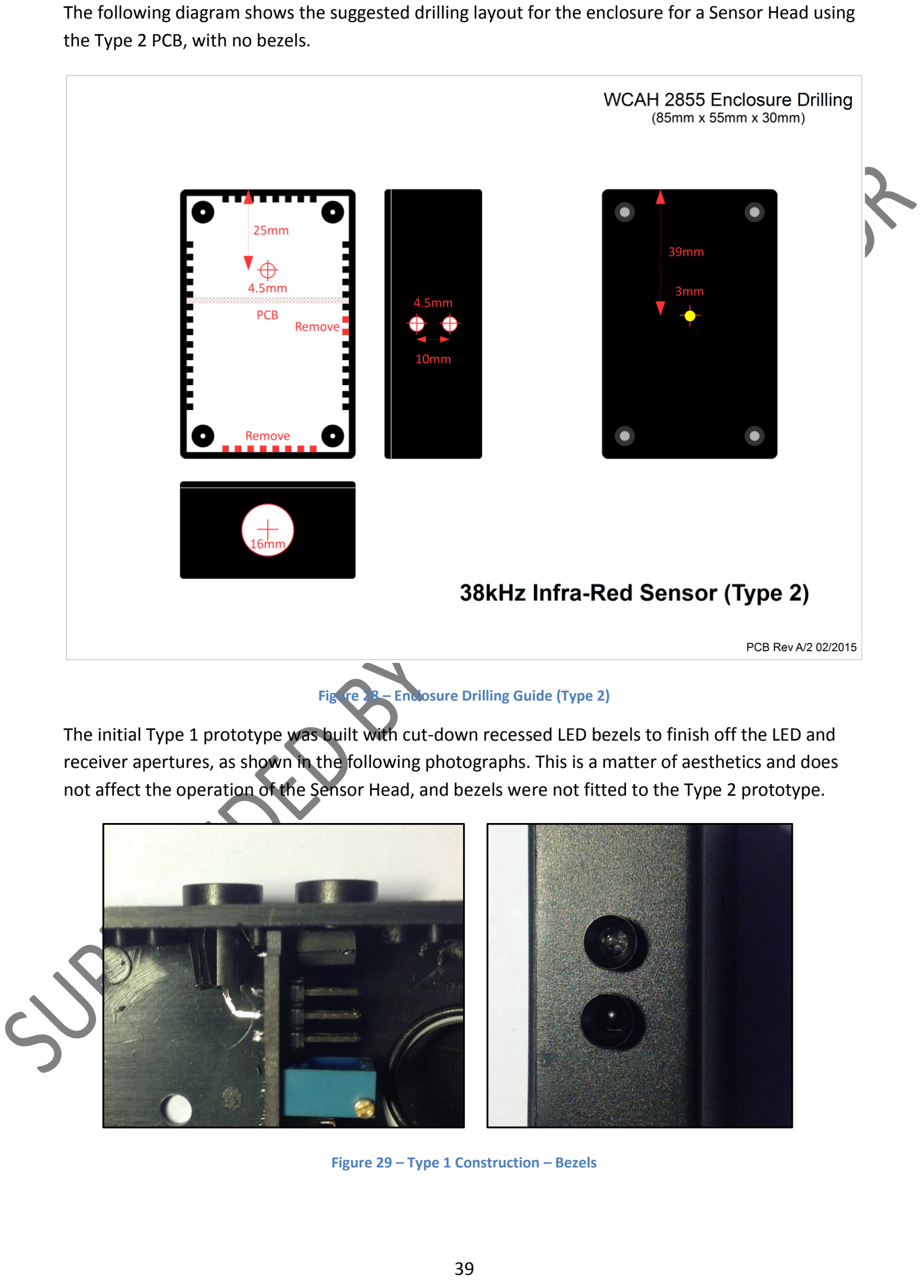
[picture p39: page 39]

The following diagram shows the suggested drilling layout for the enclosure for a Sensor Head using the Type 2 PCB, with no bezels.

Figure 28 – Enclosure Drilling Guide (Type 2)

The initial Type 1 prototype was built with cut-down recessed LED bezels to finish off the LED and receiver apertures, as shown in the following photographs. This is a matter of aesthetics and does not affect the operation of the Sensor Head, and bezels were not fitted to the Type 2 prototype.

Figure 29 – Type 1 Construction – Bezels

### Internal Wiring

A Sensor Connector Cable is required within the 38kHz infra-red Sensor Head enclosure, to connect the sensor board to the external signal connector.

Parts List
Table 7 – Internal Cabling Parts List
Component | Notes
GX16-4 Chassis Plug (Male) | Signal Connector
Ribbon Cable | 3-core
DuPont 0.1” Female Crimp Connectors | 3
DuPont 0.1” Female Connector Shell | 1 x 3-pin
While it is possible to make up the DuPont connector cables by hand, this is time consuming and not easy even if the proper crimp tool is available. An alternative approach is to buy ready-made lengths of ribbon cable with female DuPont connectors already crimped, and cut these down to make the required cables. These are readily available on eBay, and can save a lot of work.

Note that the core colours shows in this section are for clarity only, and have no other significance.

The Sensor Connector Cable has a GX16-4 chassis plug on one end, and a 3-pin female DuPont connector on the other, wired as shown the following diagram.

Figure 30 – Sensor Connector Cable Diagram

A suitable length of ribbon cable can be used for this cable, the required length is approximately 6cm overall.

The cable ends are soldered onto the GX16-4 chassis plug following the wiring the diagram above. A short length of heatshrink sleeve, 2.5mm unshrunk diameter, is recommended on each core to protect the soldered connection and provide some strain relief.

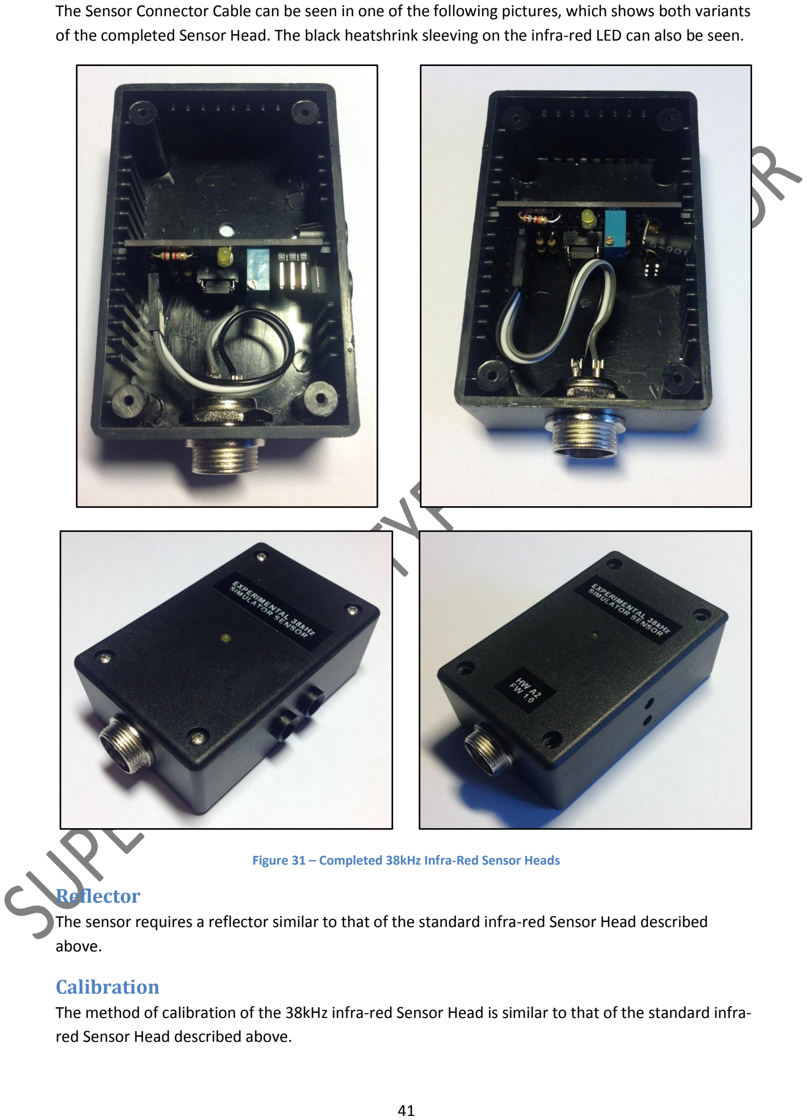
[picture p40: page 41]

The Sensor Connector Cable can be seen in one of the following pictures, which shows both variants of the completed Sensor Head. The black heatshrink sleeving on the infra-red LED can also be seen.

Figure 31 – Completed 38kHz Infra-Red Sensor Heads

### Reflector

The sensor requires a reflector similar to that of the standard infra-red Sensor Head described above.

### Calibration

The method of calibration of the 38kHz infra-red Sensor Head is similar to that of the standard infra-red Sensor Head described above.

### Installation

Installation of the Sensor Head in the belfry is similar to that of the standard infra-red Sensor Head described above.

Figure 32 – Installed Prototype 38kHz Infra-Red Sensor Head

### Firmware Upload

The firmware for the 38kHz infra-red Sensor Head released under the GNU General Public Licence (GPL), Version 3, and the source code and other supporting files can be downloaded from GitHub.

- https://github.com/Simulators/simulator/tree/master/firmware/38khzsensor

The firmware is very simple, and has only two functions:

- The onboard clock is used to generate a 38kHz PWM signal to drive the infra-red LED. Note that the values used assume that the ATtiny85 is being driven by its internal 8MHz clock.
- The main loop reads the state of the output from the infra-red receiver, and sets the state of the Sensor Head output to match. It also sets the diagnostic LED to the inverse of the IR receiver output state.

The Sensor Head firmware is held in non-volatile flash memory on the ATtiny85 microcontroller. It should only be necessary to re-upload the software in the event that the microcontroller is replaced, the flash memory has become corrupted, or the firmware requires updating.

The firmware code needs to be uploaded to the microcontroller on the 38kHz infra-red sensor PCB. The method of uploading the firmware using a hardware programmer via the ICSP header pins provided on the sensor PCB is exactly the same as that for the One Bell Simulator Interface, and is fully documented in the One Bell Simulator Interface Hardware Manual.

- The 38kHz Simulator Sensor Interface Boards (ICSP) entry must be selected in the Arduino

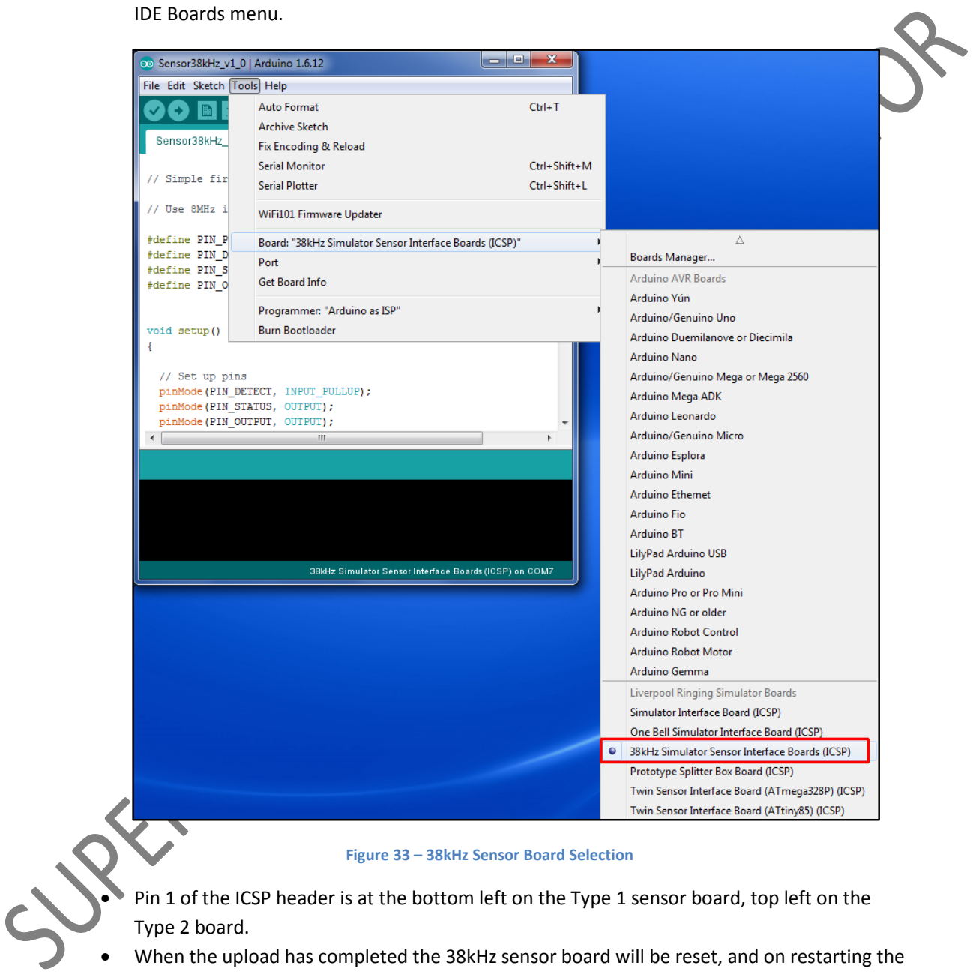
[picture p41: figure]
IDE Boards menu.; Type 2 board.

Figure 33 – 38kHz Sensor Board Selection

- Pin 1 of the ICSP header is at the bottom left on the Type 1 sensor board, top left on the
- When the upload has completed the 38kHz sensor board will be reset, and on restarting the yellow diagnostic LED will flash twice in quick succession.

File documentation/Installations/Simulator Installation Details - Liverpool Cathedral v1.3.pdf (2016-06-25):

Liverpool Ringing Simulator Project

## Simulator Installation Details

### Simulator Interface

Location | Liverpool Cathedral
Simulator Type | Multiple Bell
Sensor Channels Equipped | 12
Interface Enclosure | MB4
PCB Versions | Simulator Interface PCB – Rev B LED/Reset Board – Rev A
Firmware | Simulator Interface v2.4
Active Channels | 12
De-bounce Timer | 3ms
Power/Data Cable Length | 24m
Power Supply | 9v
Serial Port | PC RS-232 (COM1)
Simulator Software Package | Abel v3.9.1
Notes:
Tracopower TSR 1-2450 voltage regulator fitted.
Reset switch fitted.
Experimental TVS daughter board Rev A fitted (12 channels equipped).

### Sensor Heads

Bell | Sensor Head Type | Sensor Head Cable Length | Sensor Head Mounting | Delay Timer (ms / cs)
1 | Hedley Magneto-Resistive Rev A | 6.5m | Timber Batten 0.50m | 39
2 | Infra-Red – E18-D80NK | 8.8m | Timber Batten 0.51m | 41
3 | Infra-Red – E18-D80NK | 10.0m | Timber Batten 0.52m | 44
4 | Infra-Red – E18-D80NK | 11.2m | Timber Batten 0.54m | 46
5 | Infra-Red – E18-D80NK | 10.5m | Timber Batten 0.59m | 48
6 | Infra-Red – E18-D80NK | 9.3m | Timber Batten 0.60m | 51
7 | Infra-Red – E18-D80NK | 7.9m | Timber Batten 0.69m | 53
8 | Infra-Red – E18-D80NK | 6.4m | Timber Batten 0.81m | 55
9 | Infra-Red – 38kHz Rev A1 | 4.7m | Timber Batten 0.77m | 58
10 | Infra-Red – E18-D80NK | 2.7m | Timber Batten 0.79m | 60
11 | Infra-Red – E18-D80NK | 1.8m | Timber Batten 0.93m | 62
12 | Infra-Red – E18-D80NK | 4.3m | Timber Batten 1.20m | 65

### Belfry Installation

Sensor Heads
The Sensor Heads are mounted on 38mm x 22mm softwood support battens, which in turn are screwed to the pulley box beams with No10 x 50mm stainless steel pan head screws. The Sensor Heads are positioned with the connector pointing downwards to limit water ingress, and the battens are treated with a proprietary wood preservative.

A length of reflective tape is stuck to the shroud of the wheel, positioned directly opposite the sensor when the bell is down. The tape is self-adhesive, and the wheel shroud was lightly sanded and cleaned with methylated spirits to improve adhesion of the tape.

There is no Sensor Head on the Sharp 2nd bell. When the bells are silenced it does not matter which 2

nd is rung with the light eight, the correct mapping and tuning being handled in the Abel

configuration.

The following pictures show the Sensor Head installations on the treble and 11th. The reflective tape is not visible on the 11th’s wheel because the bell is up.

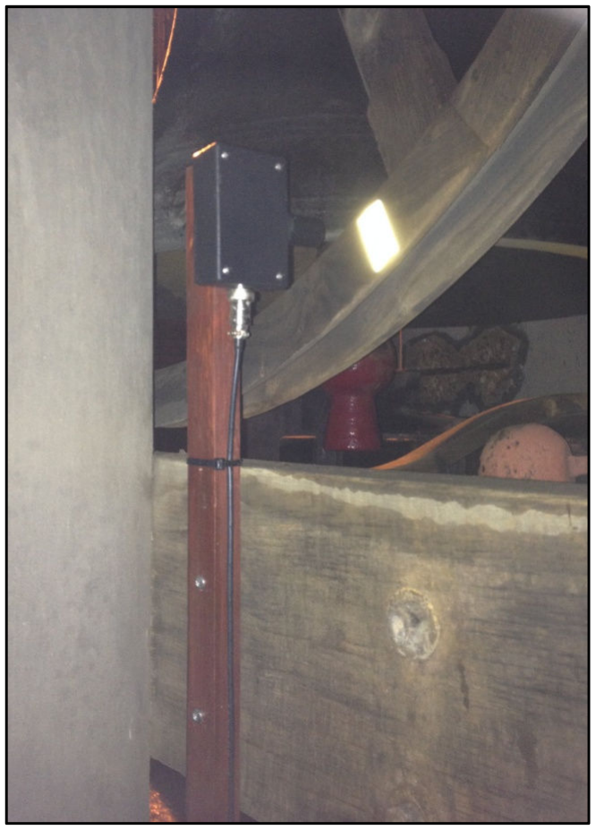
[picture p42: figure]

Treble Sensor Head | Eleventh Sensor Head

Sensor Head Cables
The Sensor Head cables are cable tied to the support battens, and run vertically down to the top surface of the circular frame plinth.

From there they run around the top of the plinth to the Simulator Interface, which is located in the pit of the 10th bell. To keep the cable runs as short as possible, cables for bells 5 – 10 run clockwise

round the frame plinth to the Simulator Interface, and the remainder run anticlockwise.

Where the bundle of cables passes each frame element, it runs through a 200mm length of 16mm x 16mm plastic trunking, which is held in place on the concrete frame by a small concrete paving block.

Simulator Interface
The Simulator Interface is located in the pit of the 10th bell. To protect it from the worst of the

weather the Interface has been placed in a secondary enclosure, with cable entry arranged so as to limit any water ingress.

The following picture shows the Simulator Interface in position.


Installed Simulator Interface

A small concrete paving block has been placed on top of the secondary enclosure to limit movement.

### Custom Tuning

Abel Sound Configuration
The samples of Worcester Cathedral bells supplied with Abel 3.8.0a onwards are used, with some configuration modifications to enable the correct lower Liverpool Cathedral pitch to be sounded.

Bell Sound Files
The 12 bell sound files from the Worcester set are used unmodified in the Bells subdirectory¹ of the
Abel installation on the Simulator PC.

Bell Description File
The original Bell Description File supplied with the Worcester samples has been modified to allow

Abel to produce simulated ringing using these sound files in the key of AH. Abel v3.9.0b only allows

the simulated bells to be tuned down to the key of A, while Liverpool Cathedral bells are in the key

of AH. This limitation does not affect any other tower, Liverpool Cathedral having the only ring of

bells tuned lower than BH. A workaround is therefore required to support tuning down to AH.

Four modifications are necessary to a copy of the Bell Description File to achieve this:

- The BDF row text has been amended to indicate that this is a modified configuration, and

Abel should be set to the key of A in order to sound as AH.

- The MIDI bottom note values (last field) for each bell sample have been adjusted downwards where required to allow all the samples to be used down to the key of A.
- The MIDI base note value for each bell has been raised by one semitone, so that the Abel will

treat the samples as though they were in the key of BH, and tunes each note sample down a

further semitone to sound the note AH when the configuration is set to A.

- The MIDI top note values have been adjusted to allow the front 6, 8 or 10 bells to be rung as simulated diatonic rings of bells, with the appropriate tenor notes. Refer to the table below.

The modified BDF file looks like this:
BDF, Worcester Custom Tuning A for Ab wr12.wav, 48, 45, 45
wr11.wav, 50, 47, 47
wr10.wav, 52, 49, 49
wr9.wav, 53, 51, 50
wr8.wav, 55, 53, 52
wr7.wav, 57, 54, 54
wr6.wav, 59, 56, 56
wr5.wav, 60, 58, 57
wr4.wav, 62, 60, 59
wr3.wav, 64, 61, 61
wr2.wav, 65, 63, 62
wr1.wav, 67, 65, 64

1
C:\Program Files\Abel 3\Bells\

Abel Sound Options
1. In Abel, select Ringing Options… from the Options menu.

### 2. In the Ringing Options window, set the Number of Bells to “12”, and the Peal Time to

“04:30” (4h 30m). Then click OK.


3. Select Sound Options… from the Options menu.
4. In the Sound Options window, set the Number of Bells to “12”, the Tenor Note to “A” (the lowest possible setting, and not “a”, which is an octave higher), and in the Bell Sound field select the modified Worcester Custom Tuning file. Then Click OK.


5. Save the new options by selecting Save Options from the Options menu. If the options have changed, Abel will prompt you to do this when the program is closed.
6. Abel is now configured to produce simulated ringing in the key of AH.

Simulated Diatonic Rings
The following table shows the Abel sound tuning and MIDI note values used in the Liverpool Cathedral Simulator to allow simulated diatonic rings of bells using the back 8, 10 or 12 bells, or the front 6, 8 or 10 bells.

In all cases the simulated bells sound a semitone lower than the values below configured in Abel.

All true diatonic rings of six are also shaded.

Accidentals which are not part of the real Cathedral diatonic ring of 12 are shown in bold.

Bell | The 12 | Front 10 | Front 8 | Front 6 | Back 10 | Back 8 | Abel BDF MIDI Values
Note | MIDI | Note | MIDI | Note | MIDI | Note | MIDI | Note | MIDI | Note | MIDI | Top | Bott om
1 | E | 64 | EG | 65 | E | 64 | EG | 65 | | | | | 65 | 64
2 | D | 62 | DG | 63 | DG | 63 | DG | 63 | | | | | 63 | 62
3 | CG | 61 | CG | 61 | CG | 61 | CG | 61 | CG | 61 | | | 61 | 61
4 | B | 59 | BG | 60 | B | 59 | BG | 60 | B | 59 | | | 60 | 59
5 | A | 57 | AG | 58 | A | 57 | AG | 58 | A | 57 | A | 57 | 58 | 57
6 | GG | 56 | GG | 56 | GG | 56 | GG | 56 | GG | 56 | GG | 56 | 56 | 56
7 | FG | 54 | FG | 54 | FG | 54 | | | FG | 54 | FG | 54 | 54 | 54
8 | E | 52 | EG | 53 | E | 52 | | | E | 52 | E | 52 | 53 | 52
9 | D | 50 | DG | 51 | | | | | D | 50 | D | 50 | 51 | 50
10 | CG | 49 | CG | 49 | | | | | CG | 49 | CG | 49 | 49 | 49
11 | B | 47 | | | | | | | B | 47 | B | 47 | 47 | 47
12 | A | 45 | | | | | | | A | 45 | A | 45 | 45 | 45

### Quick Reference

The following quick reference shows how to set up Abel in the tower for simulated diatonic rings of bells, using the pre-defined configurations and desktop icons.

No Simulated Ringers
All the bells are rung by real ringers (for example, for demonstration or silent practice); Abel only provides simulated bell sounds.
To Ring… | Start Abel by… | Then…
All 12 | Double-click the Abel LivCath12 icon. | Ring bells 1 – 12 (using 2J, not 2G)
Back 8 | Double-click the Abel LivCath12 icon. | Ring bells 5 – 12
Back 10 | Double-click the Abel LivCath12 icon. | Ring bells 3 – 12
Front 6 | Double-click the Abel LivCath12 icon. Then File… Open… 6bell.mcf | Ring bells 1 – 6 (using 2J, not 2G)
Front 8 | Double-click the Abel LivCath12 icon. The File… Open… 8bell.mcf | Ring bells 1 – 8 (using 2J, not 2G)
Front 10 | Double-click the Abel LivCath12 icon. Then File… Open… 10bell.mcf | Ring bells 1 – 10 (using 2J, not 2G)

With Simulated Ringers
One or more bells are rung by real ringers (for example, for tenor covering practice); Abel provides simulated bell sounds, and method ringing for the remaining bells.
To Ring… | Start Abel by… | Then…
All 12 | Double-click the Abel LivCath12 icon. Then File… Open… 12bell.mcf or File… Open… 11bell.mcf for Maximus or Cinques respectively. | Select method and enable Auto-Start (F10)
Back 8 | Double-click the Abel LivCathBack8 icon. Then File… Open… 8bell.mcf or File… Open… 7bell.mcf for Major or Triples respectively. | Select method and enable Auto-Start (F10)
Back 10 | Double-click the Abel LivCathBack10 icon. Then File… Open… 10bell.mcf or File… Open… 9bell.mcf for Royal or Caters respectively. | Select method and enable Auto-Start (F10)

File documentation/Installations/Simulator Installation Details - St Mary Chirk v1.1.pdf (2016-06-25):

Liverpool Ringing Simulator Project

## Simulator Installation Details

### Simulator Interface

Location | St Mary, Chirk
Simulator Type | Multiple Bell
Sensor Channels Equipped | 6
Interface Enclosure | MB7
PCB Versions | Simulator Interface PCB – Rev B LED/Reset Board – Rev A
Firmware | Simulator Interface v2.4
Active Channels | 6
De-bounce Timer | 3ms
Power/Data Cable Length | 14m
Power Supply | 9v
Serial Port | USB-Serial Adapter (Prolific)
Simulator Software Package | Abel v3.9.0b
Notes:
Reset switch fitted.
Simulator Interface wired for dual-headed Sensors Heads; Channels 1+2 on input connector #1, channels 5+6 on input connector #5.
4-Core cable is used for the dual-headed Sensor Heads on 1+2, and 5+6.
Experimental TVS daughter board Rev A fitted (first 6 channels equipped).

### Sensor Heads

Bell | Sensor Head Type | Sensor Head Cable Length | Sensor Head Mounting | Delay Timer (ms / cs)
1 | Infra-Red – E18-D80NK | 5.5m (4-Core) | Frame (Cable Tie) | 43
2 | Infra-Red – E18-D80NK | | | 44
3 | Infra-Red – E18-D80NK | 8.0m | Frame (Cable Tie) | 45
4 | Infra-Red – E18-D80NK | 6.5m | Frame (Cable Tie) | 46
5 | Infra-Red – E18-D80NK | 3.5m (4-Core) | Frame (Cable Tie) | 47
6 | Infra-Red – E18-D80NK | | | 48
7 | - | - | - | -
8 | - | - | - | -
9 | - | - | - | -
10 | - | - | - | -
11 | - | - | - | -
12 | - | - | - | -

### Belfry Installation

Sensor Heads
The Sensor Heads are mounted on softwood support brackets, which are secured to the frame members with cable ties. The Sensor Heads are positioned with the connector pointing downwards to limit water ingress, and the brackets are treated with a proprietary wood preservative. Because the wheels have been treated with a reflective aluminium primer, some of the brackets are cantilevered out from the frame to increase the distance between sensor and reflector.

A length of reflective tape is stuck to the shroud of the wheel, positioned directly opposite the sensor when the bell is down. The tape is self-adhesive, and the wheel shroud was lightly sanded and cleaned with methylated spirits to improve adhesion of the tape.

Dual-headed Sensor Heads are installed on the treble and 2nd, and the 5th and tenor. The following

pictures show the dual-headed Sensor Heads.


Treble/Second Sensor Head | Fifth/Tenor Sensor Head


Third Sensor Head | Fourth Sensor Head

Simulator Interface
The Simulator Interface is located next to the frame in an alcove below the louvres in one corner of the tower, and the Power/Data Cable runs down to the ringing room through the disused clock weight shaft. To protect it from the worst of the weather the Interface has been placed in a secondary enclosure, with cable entry arranged so as to limit any water ingress.

The following picture shows the Simulator Interface in position.


Installed Simulator Interface

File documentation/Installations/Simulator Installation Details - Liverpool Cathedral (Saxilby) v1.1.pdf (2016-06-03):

## Simulator Installation Details

### Simulator Interface

Location | Liverpool Cathedral (Saxilby)
Simulator Type | Multiple Bell
Sensor Channels Equipped | 6
Interface Enclosure | Gewiss GW44426 (150 x 110 x 70mm)
PCB Versions | Simulator Interface PCB – Rev B (No LED/Reset Board)
Firmware | Simulator Interface v2.4
Active Channels | 6
De-bounce Timer | 3ms
Power/Data Cable Length | 12m
Power Supply | 9v
Serial Port | USB-Serial Adapter (Prolific) (COM2)
Simulator Software Package | Abel v3.9.1
Notes:
Saxilby Simulators.
LEDs mounted on Simulator Interface PCB.
No reset switch fitted.
Shares PC with 12-bell Liverpool Cathedral Simulator.

### Sensor Heads

Bell | Sensor Head Type | Sensor Head Cable Length | Sensor Head Mounting | Delay Timer (ms / cs)
1 | Hedley Magneto-Resistive Rev B | 0.4m | Frame leg (screw) | 45
2 | Hedley Magneto-Resistive Rev B | 3.15m | Frame leg (screw) | 45
3 | Hedley Magneto-Resistive Rev B | 3.1m | Frame leg (screw) | 45
4 | Hedley Magneto-Resistive Rev B | 5.15m | Frame leg (screw) | 45
5 | Hedley Magneto-Resistive Rev B | 2.4m | Frame leg (screw) | 45
6 | Hedley Magneto-Resistive Rev B | 2.6m | Frame leg (screw) | 45
7 | - | - | - | -
8 | - | - | - | -
9 | - | - | - | -
10 | - | - | - | -
11 | - | - | - | -
12 | - | - | - | -

### Belfry Installation

Sensor Heads
The Sensor Heads are mounted on the legs of the Saxilby Simulator units with No8 x ¾” stainless steel pan head screws.

The N52 grade Neodymium trigger magnets are 20mm diameter x 10mm thick, and are attached to one corner of the Saxilby weight plate.

Simulator Interface
The Simulator Interface is screwed to the supporting platform with No8 x ¾” stainless steel pan head screws.

Layout Diagram


Saxilby Simulator Layout Diagram


Installation
The following pictures show the Saxilby Simulator installation.

Saxilby Simulator Installation

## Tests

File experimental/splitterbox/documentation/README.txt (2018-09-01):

Prototype Simulator Splitter Box

Allows up to 6 PCs to be connected to one Simulator Interface.
 - PCs are USB connected, USB-A powers the splitter box PCB, so is always connected.
 - PCs on USB-B to USB-F do not power the splitter.
 - Interface is RS232 connected, NOT powered off the splitter box PCB (so uses a std cable and PSU).
 - Uses standard FTDI USB Virtual COM Port drivers.

3 Modes of operation:

Pass-Through : 
 - 2-way IO between the Simulator Interface RS232 port and the PC on USB-A
 - LED is Red.
 - Conventional simulator operation, allows the Interface to be configured from the PC (e.g.
   Abel delays, CLI commands).

Shared : 
 - Data incoming from the Simulator Interface RS232 port is distributed and remapped
   to all USB ports.
 - So physical bell 1 can be signal 1 on USB-A, physical bell 2 can be a signal
   on USB-B (including being remapped to signal 1), etc, etc.
 - LED is Green.
 - In the current code in this mode the USB ports are never read, but the lines are wired
   up on the PCB.
 - Supports remapping to bells IDs 13-16 (ABCD) and switch signals (WXYZ). 

Config : 
 - 2-way IO between the Splitter Box firmware and the PC on USB-A.
 - LED is flashing green/red.
 - CLI commands for configuring the Splitter Box firmware, signal mappings and so on. 

Refer to the source code for more details.

Prototype is functional, but requires more work to get to a usable product.
Could perhaps be expanded to support more USB ports by creating a custom "transmit-only"
version of SoftwareSerial for ports other than USB-A.

PCB: https://oshpark.com/shared_projects/ameUqaLq

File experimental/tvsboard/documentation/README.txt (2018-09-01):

An experimental daughter board for the Simulator Interface Board.

One of the shortcomings of the original Simulator Interface Board is the lack of
TVS protection against induced voltage spikes on the signal and power supply lines between
the Sensor Heads and the Simulator Interface.

This experimental board provides TVS protection for these connections in the form of
a daughter board which can be mounted on the Simulator Interface Board sensor connector,
and provides protected connections for the sensors.

The board is mounted onto the Simulator Interface Board with two male-to-female M3 threaded
nylon spacers, 12mm long, and suitable nylon M3 pan head screws and nuts.

The component used is the SA5.0A uni-directional TVS diode from Littlefuse, one per sensor line.

This is suitable for Simulator Interface board Rev C. It is not required for Rev D boards which incorporate the diodes on the main PCB.

PCB: https://oshpark.com/shared_projects/2v4dNsRr

AIC
15/08/2016

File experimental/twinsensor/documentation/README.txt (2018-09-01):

A very experimental magneto-resistive twin-detector sensor.

Still under early development and testing, more documentation to follow.

AIC
25/6/2016

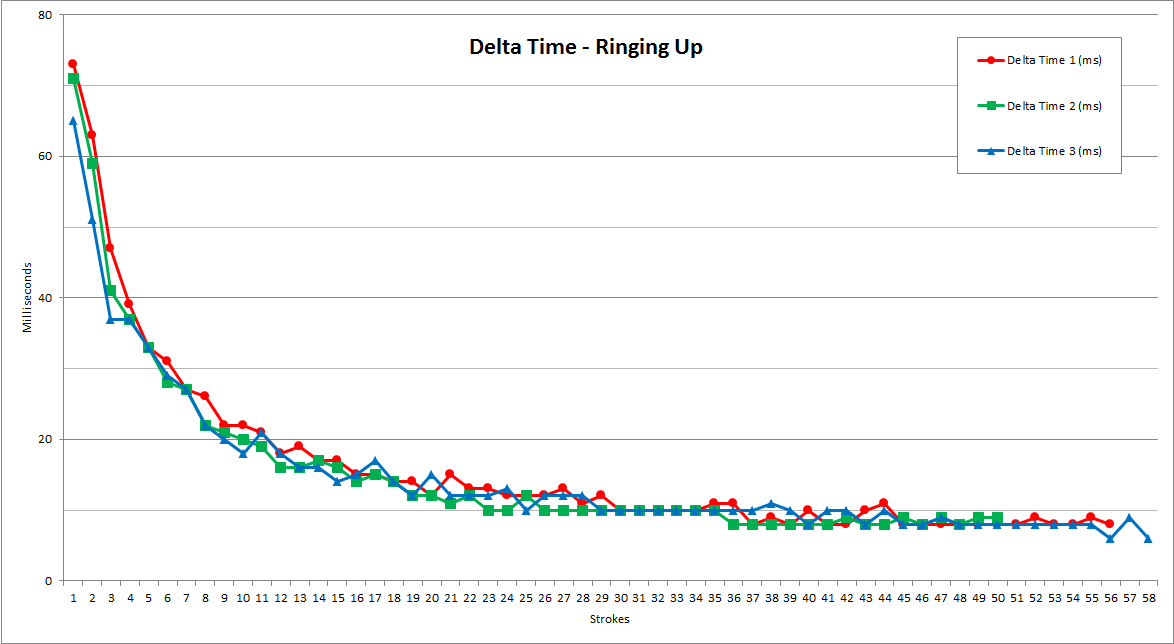
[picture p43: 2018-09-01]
experimental/twinsensor/documentation/Images/ringing_up_deltas.png

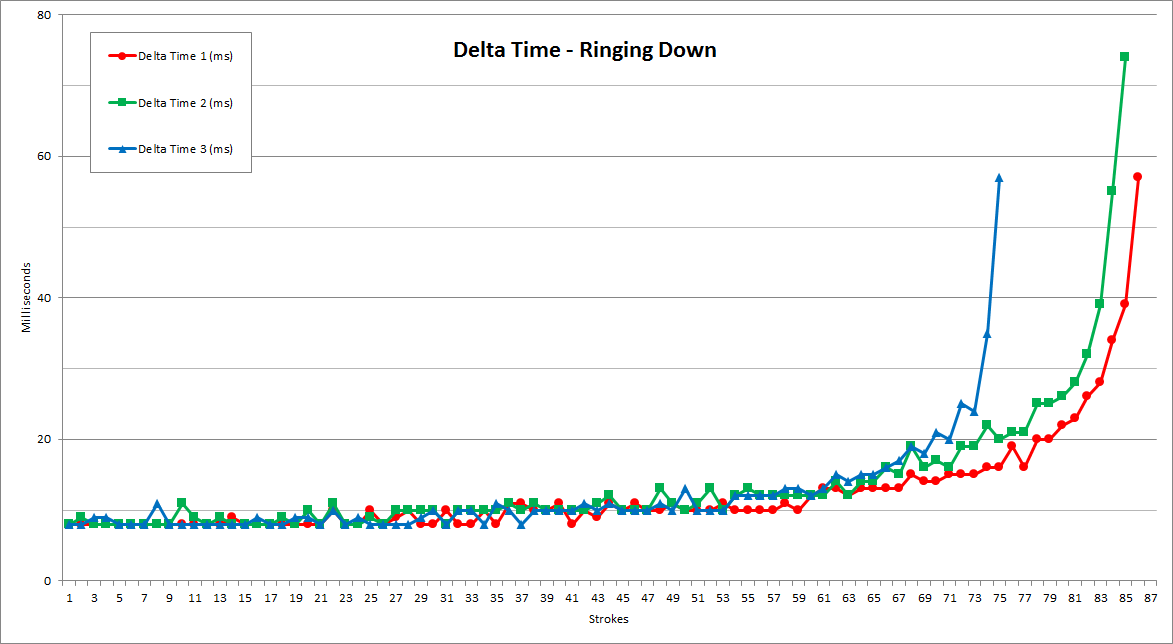
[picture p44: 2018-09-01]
experimental/twinsensor/documentation/Images/ringing_down_deltas.png

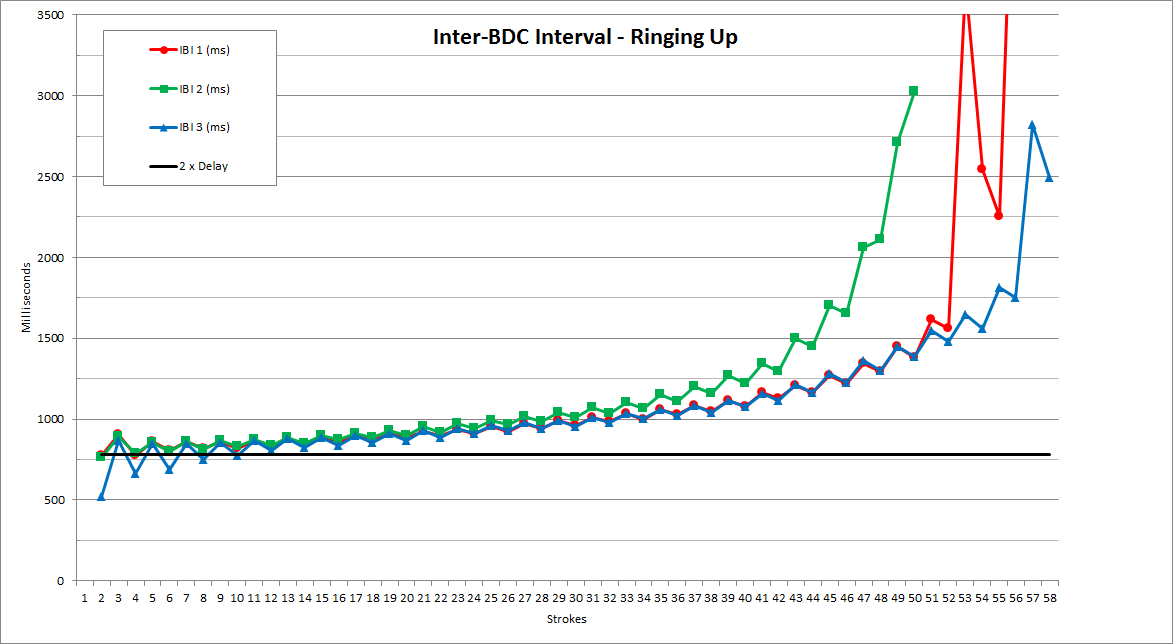
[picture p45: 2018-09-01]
experimental/twinsensor/documentation/Images/ringing_up_bdc.png

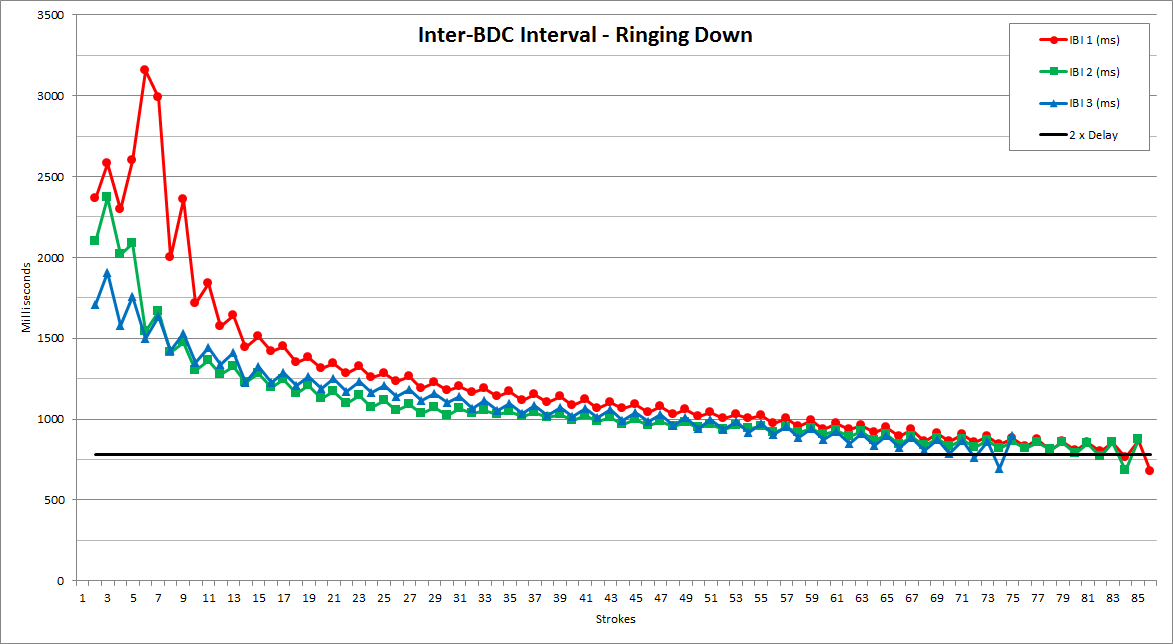
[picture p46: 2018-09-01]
experimental/twinsensor/documentation/Images/ringing_down_bdc.png

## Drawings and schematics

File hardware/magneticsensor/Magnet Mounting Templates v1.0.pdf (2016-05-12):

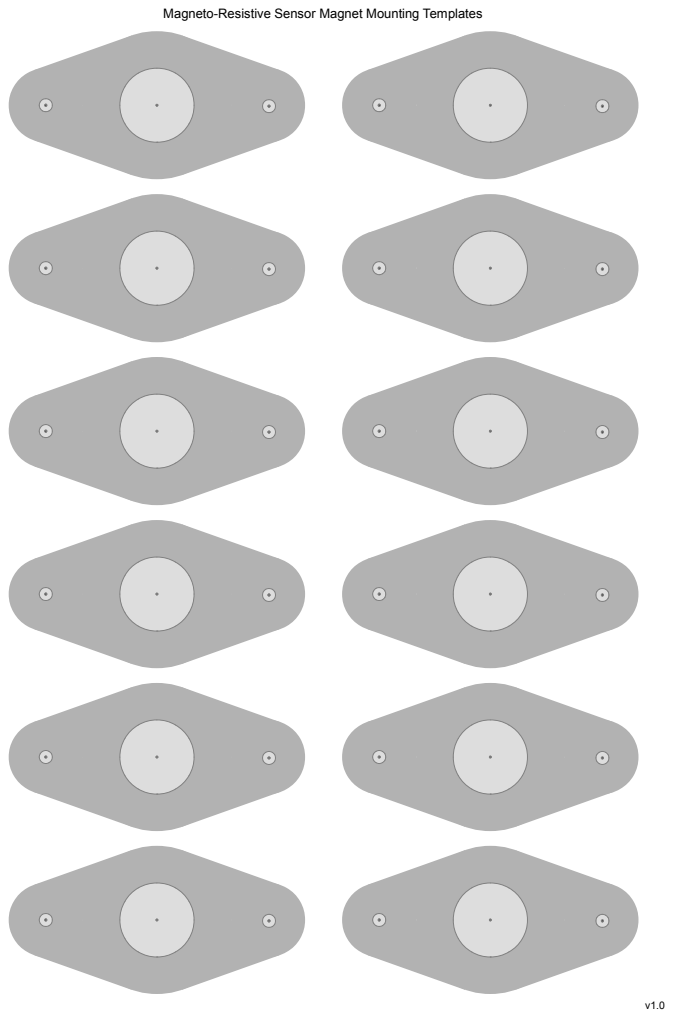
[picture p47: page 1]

Magneto-Resistive Sensor Magnet Mounting Templates

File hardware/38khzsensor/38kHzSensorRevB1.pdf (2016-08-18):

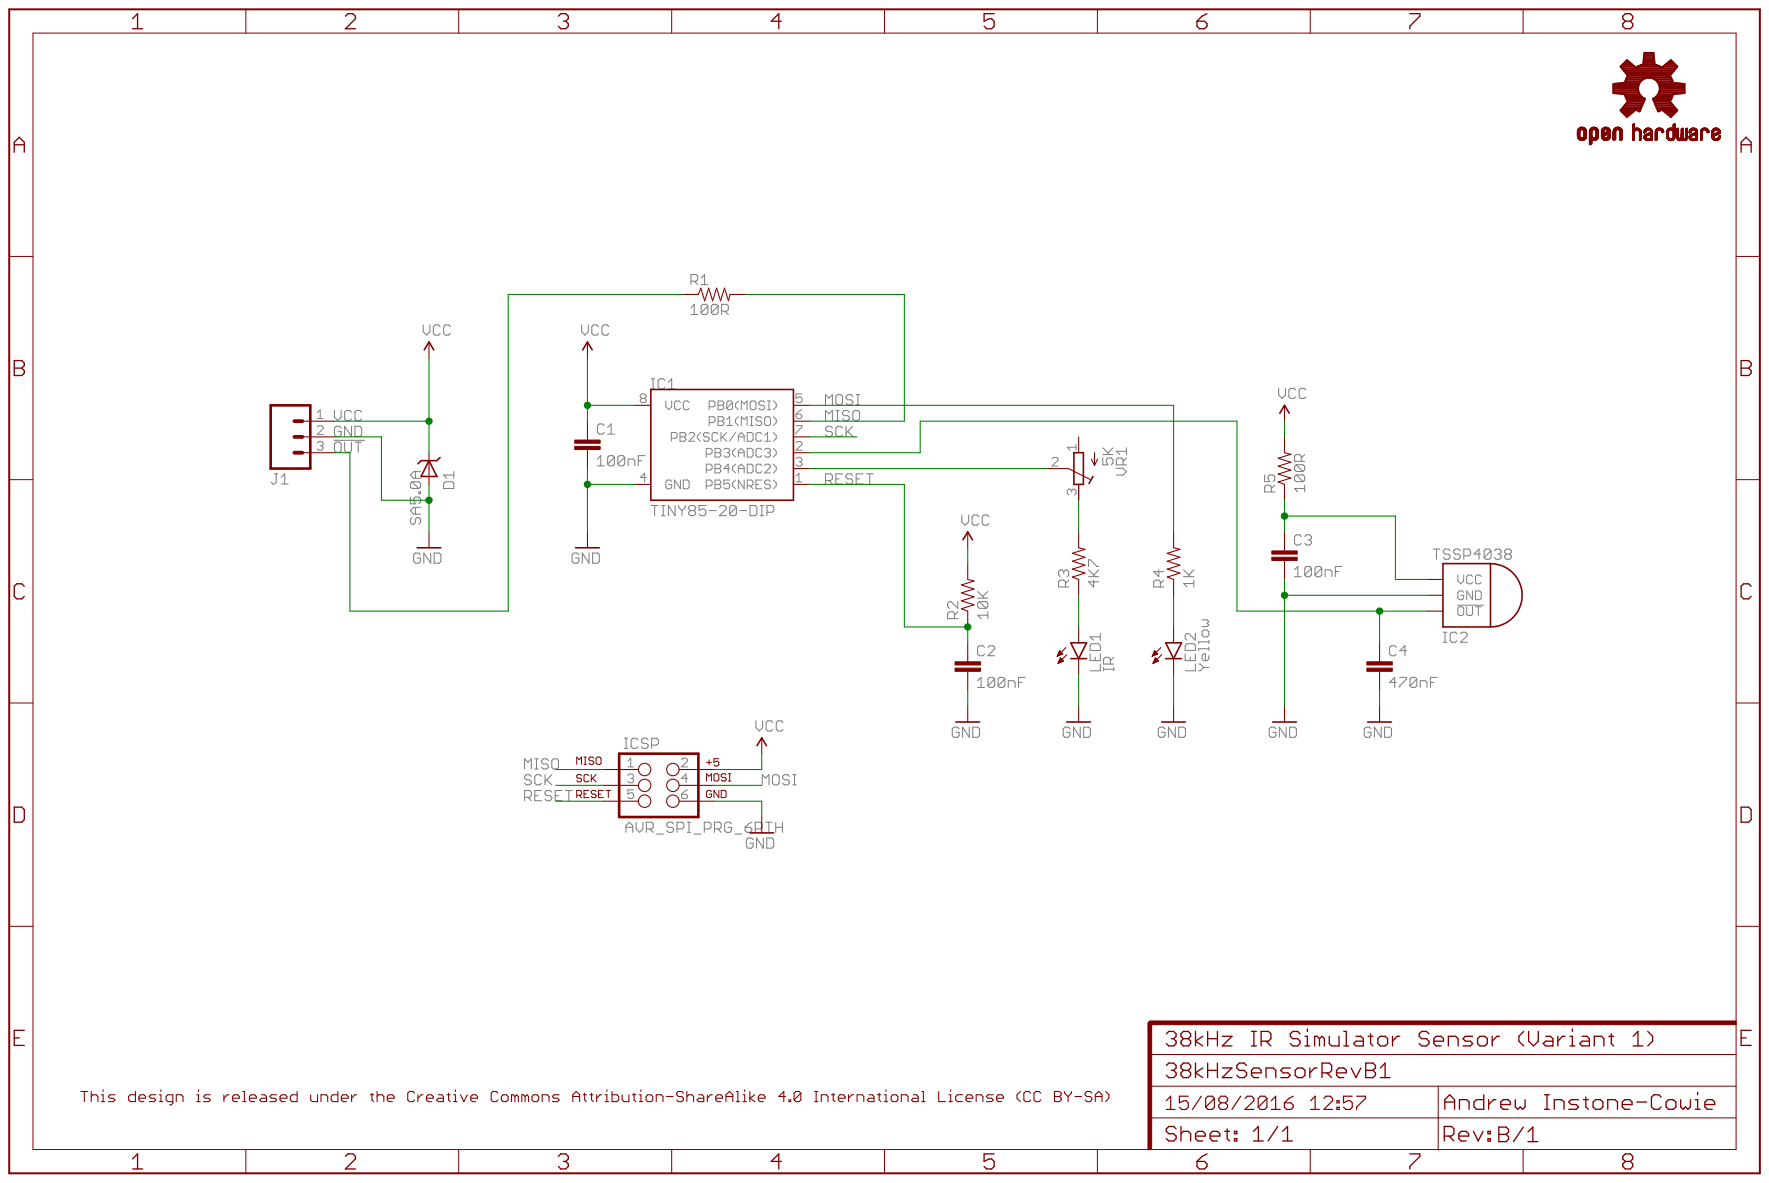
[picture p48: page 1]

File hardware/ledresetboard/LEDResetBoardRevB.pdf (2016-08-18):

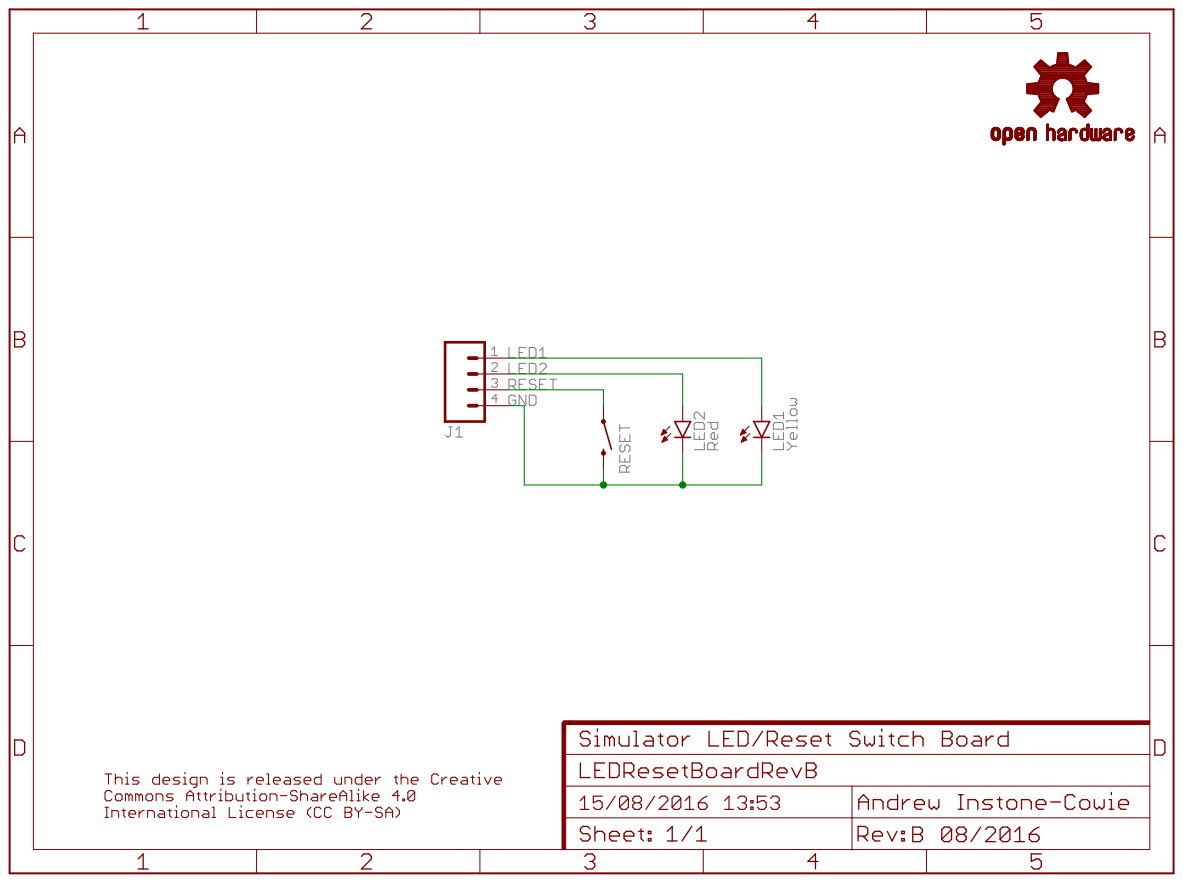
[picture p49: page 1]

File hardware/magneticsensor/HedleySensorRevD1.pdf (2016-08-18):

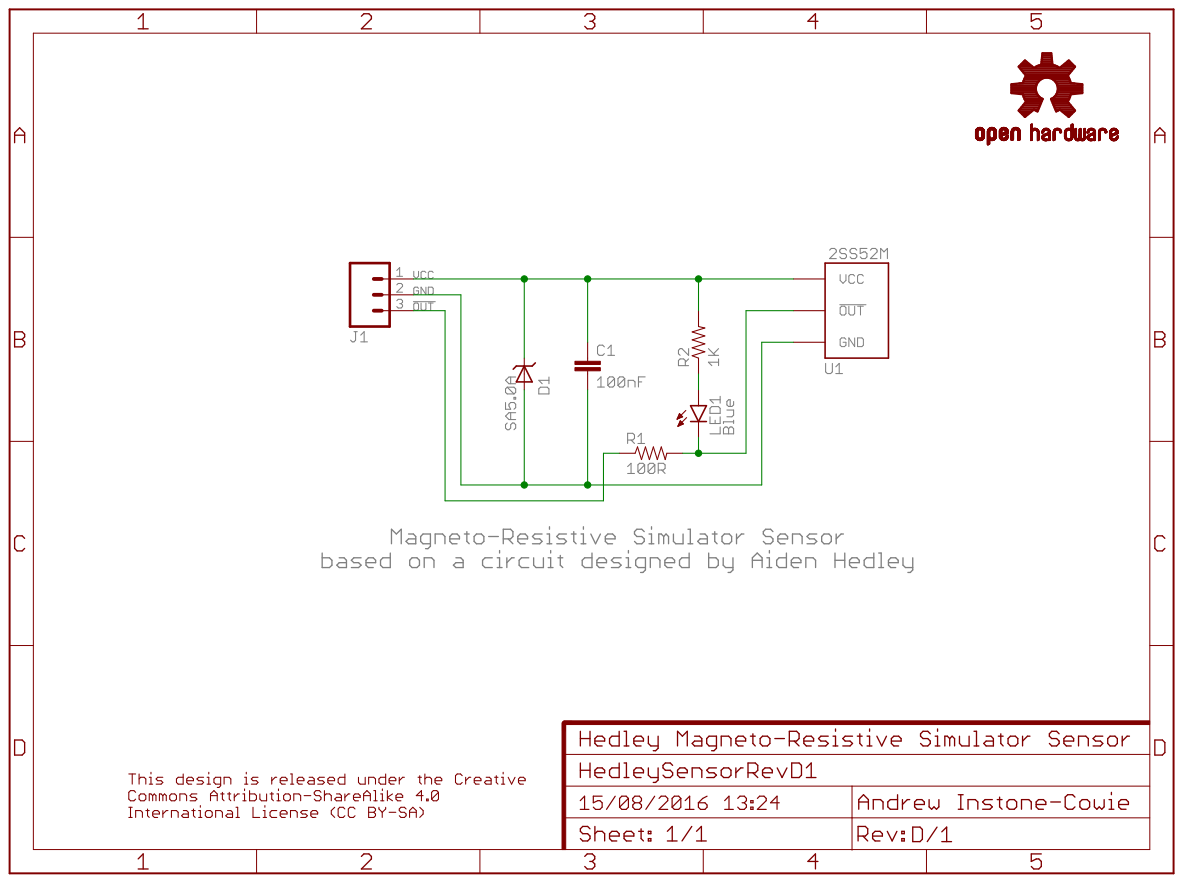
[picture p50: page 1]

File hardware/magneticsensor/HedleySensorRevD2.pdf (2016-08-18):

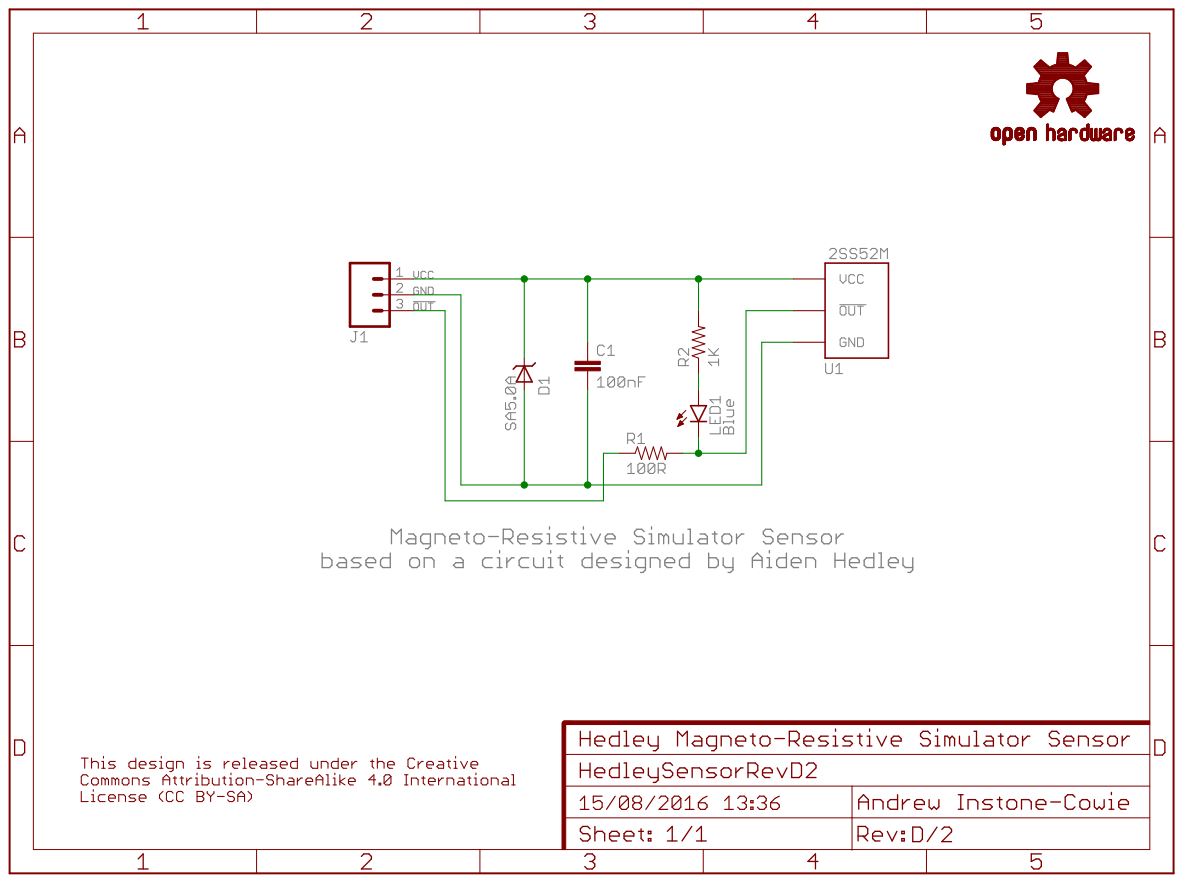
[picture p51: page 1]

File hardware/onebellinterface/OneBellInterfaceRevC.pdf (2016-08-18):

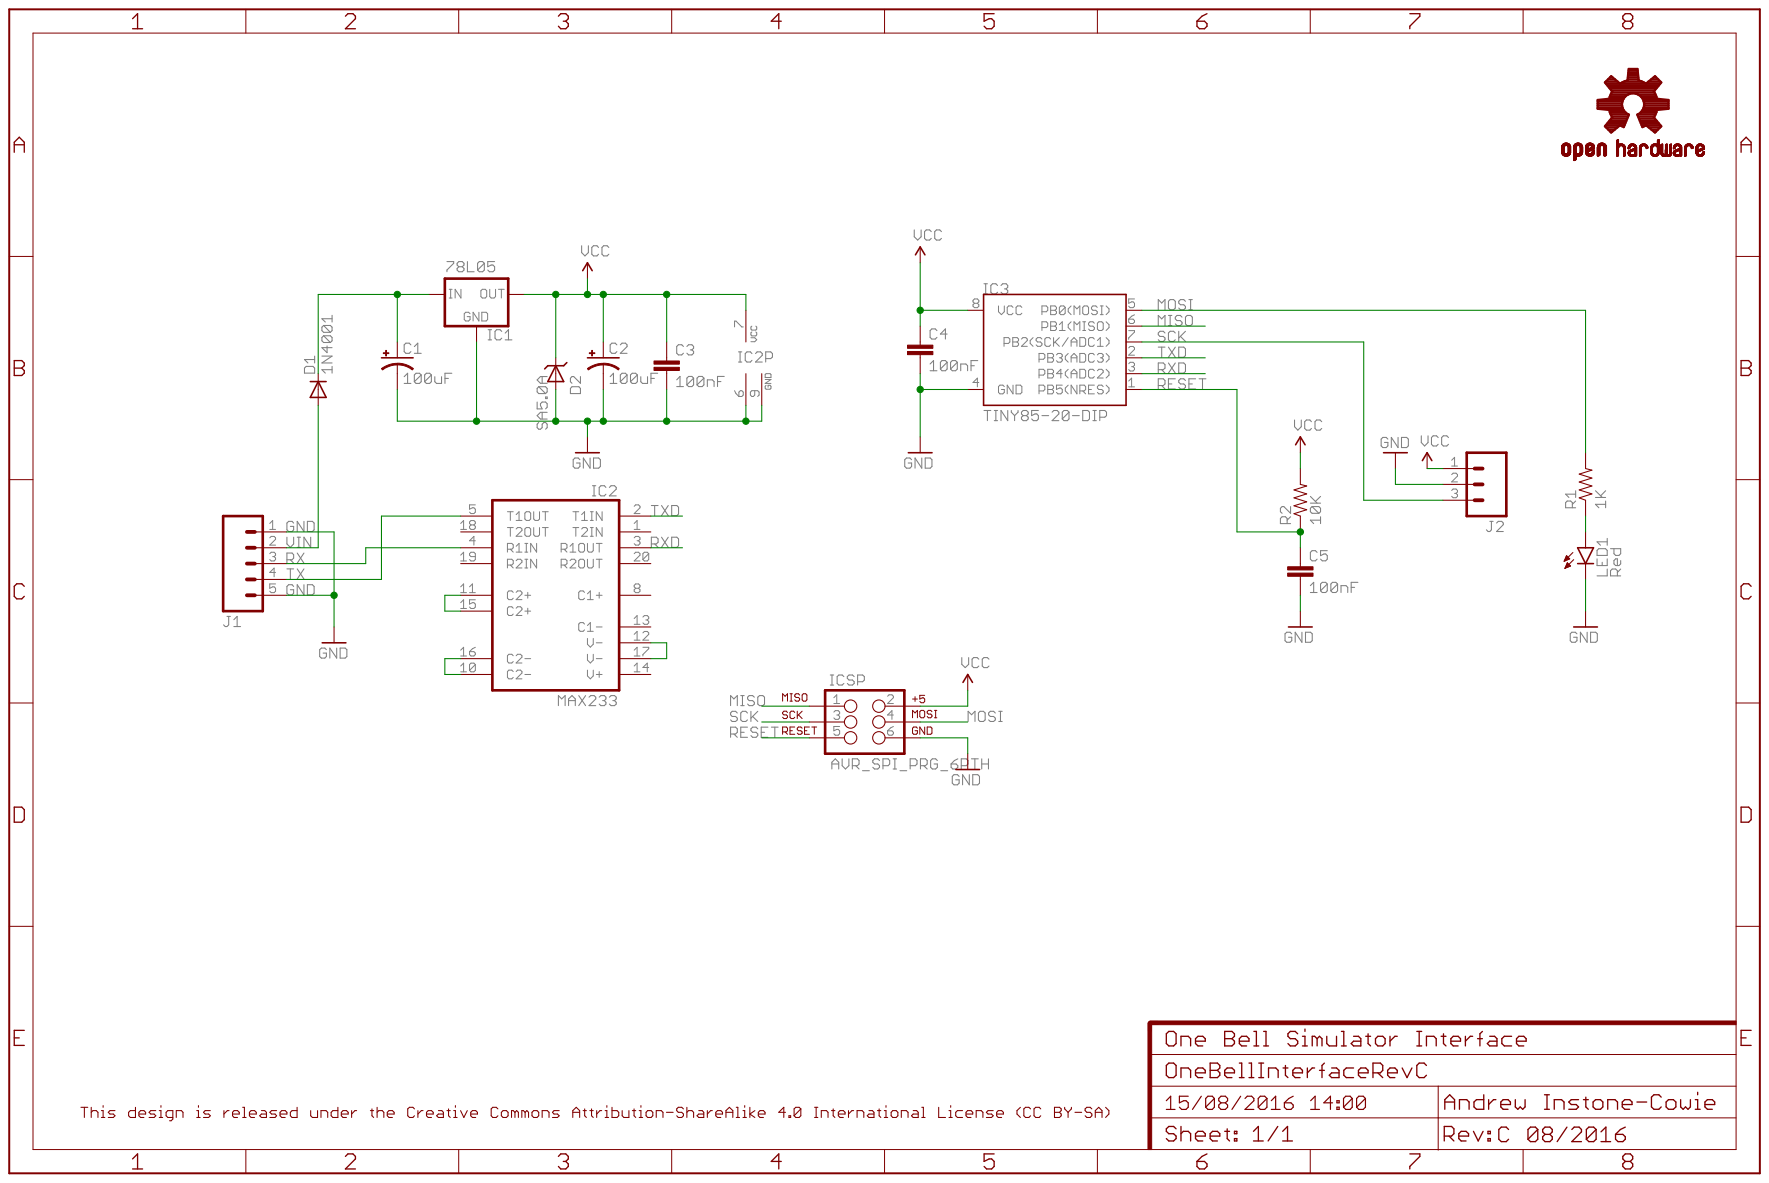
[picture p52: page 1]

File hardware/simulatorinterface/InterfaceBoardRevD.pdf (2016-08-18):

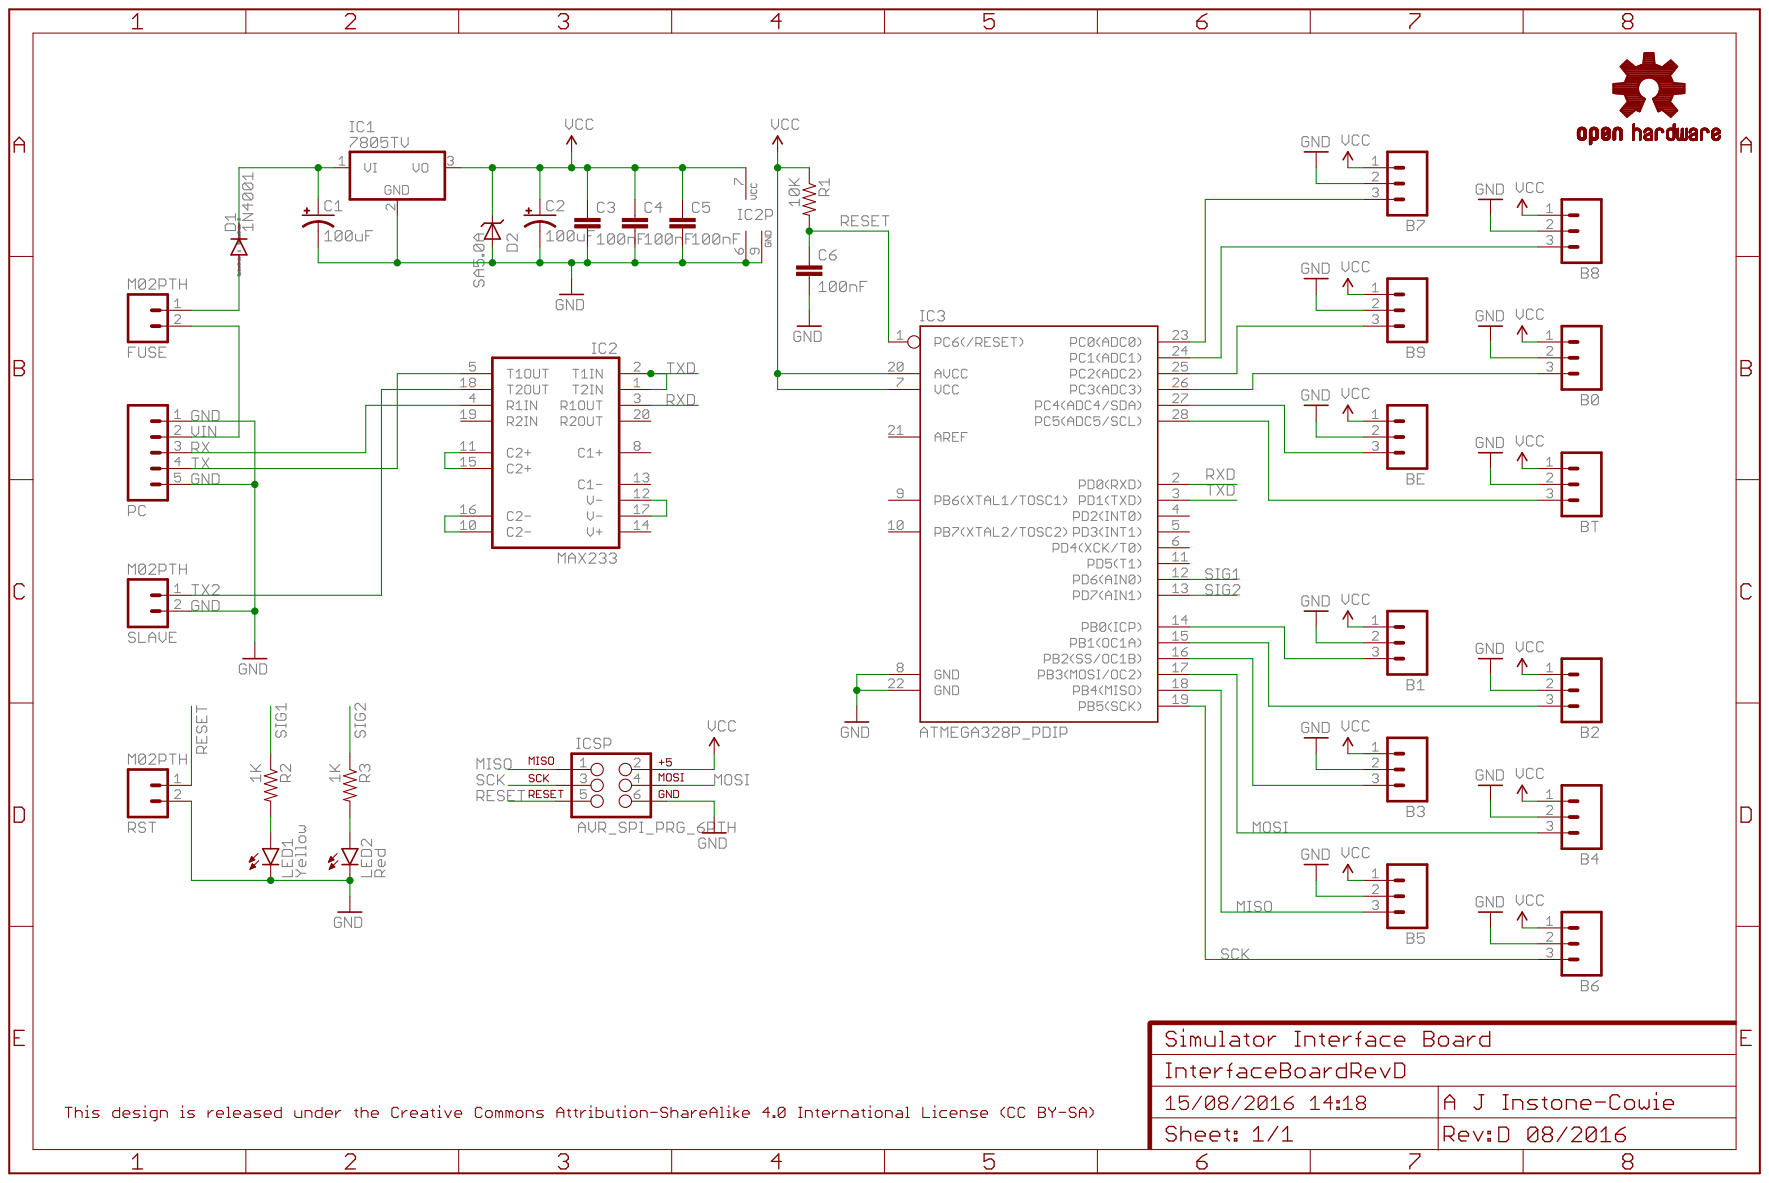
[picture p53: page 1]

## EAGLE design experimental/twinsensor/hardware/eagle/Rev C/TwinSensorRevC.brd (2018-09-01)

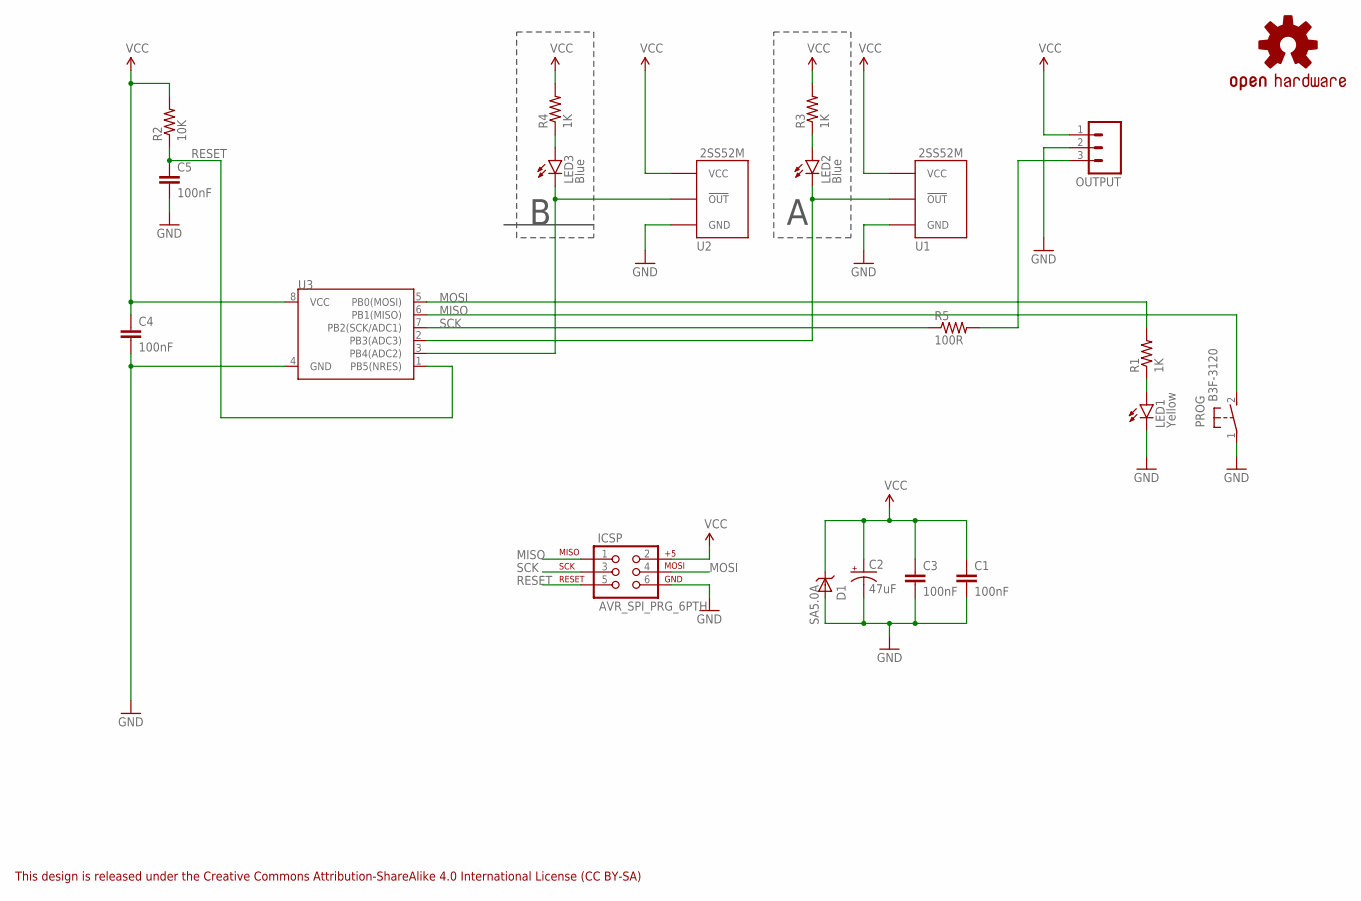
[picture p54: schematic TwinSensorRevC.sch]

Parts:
C1, C3, C4, C5: 100nF; CAP-PTH-SMALL
C2: 47uF; CPOL-RADIAL-100UF-25V
D1: SA5.0A; DO41_TVS_UNI
ICSP: AVR_SPI_PRG_6PTH; 2X3
LED1: Yellow; LED3MM
LED2, LED3: Blue; LED3MM
LOGO1: OSHW-LOGOS; OSHW-LOGO-S
OUTPUT: M03PTH; 1X03
PROG: B3F-3120
R1, R3, R4: 1K; AXIAL-0.4
R2: 10K; AXIAL-0.4
R5: 100R; AXIAL-0.4
U1, U2: 2SS52MVERT; 2SS52M_VERT
U3: ATTINY45DIL08_LONG_PADS; DIL08

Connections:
GND: C1.2, C2.2 (-), C3.2, C4.2, C5.2, D1.ANODE, ICSP.6, LED1.K (C), OUTPUT.2, PROG.1, U1.P$1 (GND), U2.P$1 (GND), U3.4 (GND)
MISO: ICSP.1, PROG.2 (S), U3.6 (PB1(MISO))
MOSI: ICSP.4, R1.P$2 (2), U3.5 (PB0(MOSI))
unnamed: LED2.A, R3.P$1 (1)
unnamed: LED3.A, R4.P$1 (1)
unnamed: LED1.A, R1.P$1 (1)
unnamed: LED2.K (C), U1.P$2 (!OUT!), U3.2 (PB3(ADC3))
unnamed: LED3.K (C), U2.P$2 (!OUT!), U3.3 (PB4(ADC2))
OUT: OUTPUT.3, R5.P$2 (2)
RESET: C5.1, ICSP.5, R2.P$1 (1), U3.1 (PB5(NRES))
SCK: ICSP.3, R5.P$1 (1), U3.7 (PB2(SCK/ADC1))
VCC: C1.1, C2.1 (+), C3.1, C4.1, D1.CATHODE, ICSP.2, OUTPUT.1, R2.P$2 (2), R3.P$2 (2), R4.P$2 (2), U1.P$3 (VCC), U2.P$3 (VCC), U3.8 (VCC)

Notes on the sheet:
This design is released under the Creative Commons Attribution-ShareAlike 4.0 International License (CC BY-SA)

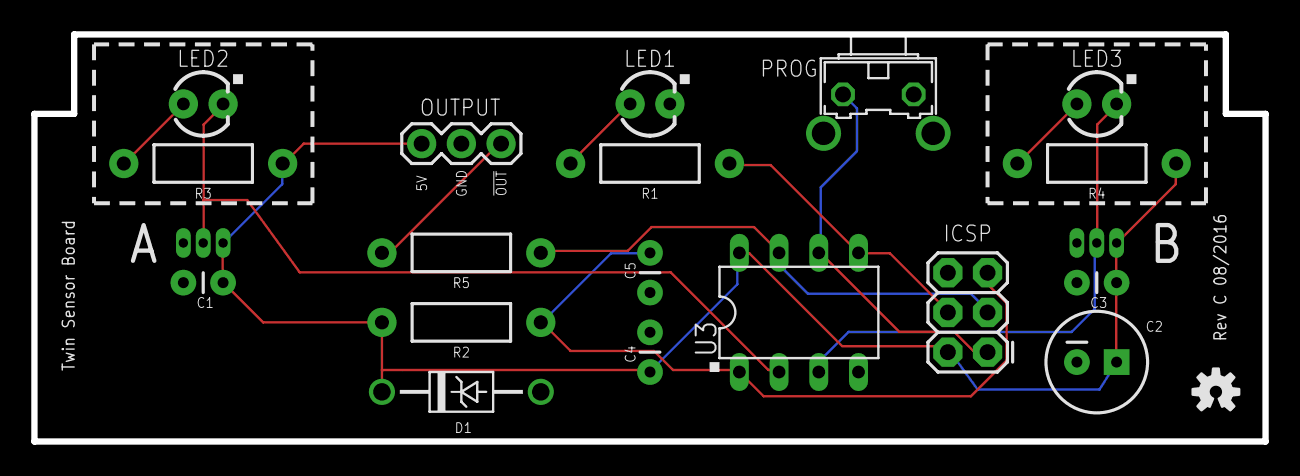
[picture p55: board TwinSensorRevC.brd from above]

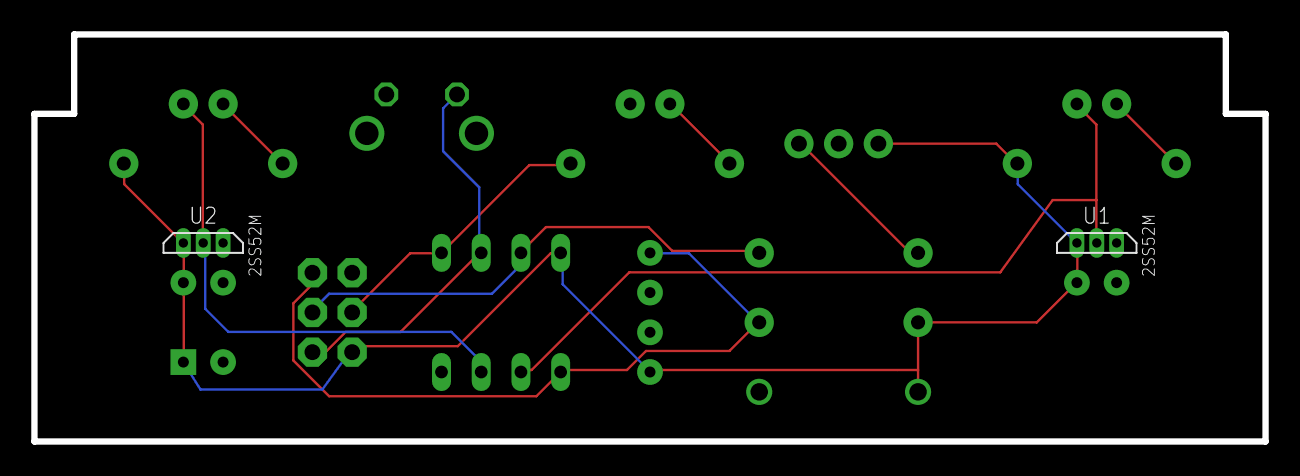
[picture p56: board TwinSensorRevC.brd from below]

Board: 2 copper layers, 78.7 x 26.0 mm, 21 parts (2 on the bottom side), 12 nets.

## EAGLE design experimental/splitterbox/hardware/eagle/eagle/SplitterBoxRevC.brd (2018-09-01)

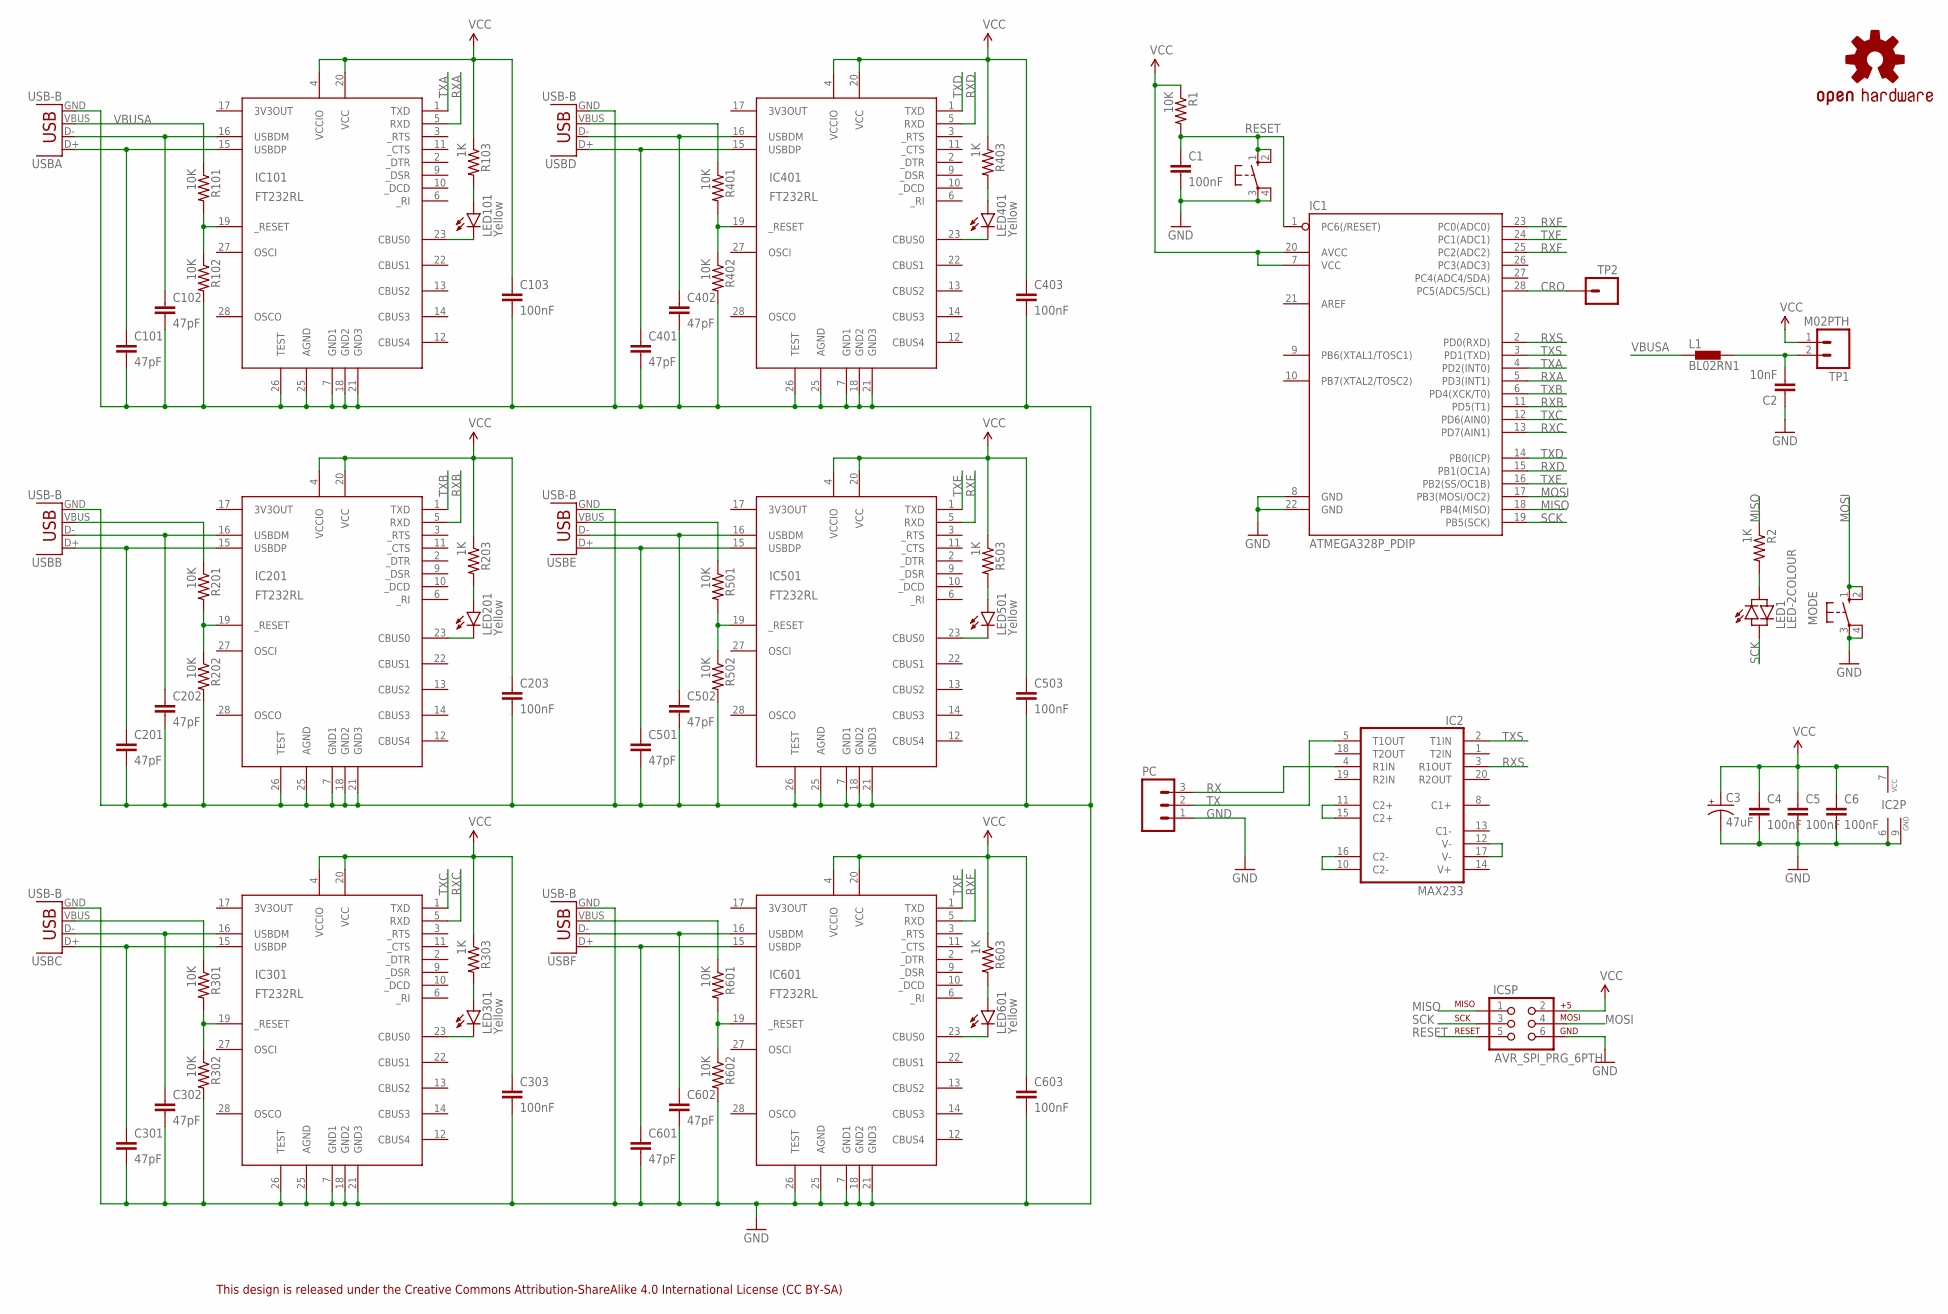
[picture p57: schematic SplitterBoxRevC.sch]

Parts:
C1, C4, C5, C6, C103, C203, C303, C403, C503, C603: 100nF; CAP-PTH-SMALL
C2: 10nF; CAP-PTH-SMALL
C3: 47uF; CPOL-RADIAL-100UF-25V
C101, C102, C201, C202, C301, C302, C401, C402, C501, C502, C601, C602: 47pF; CAP-PTH-SMALL
IC1: ATMEGA328P_PDIP; DIL28-3
IC2: MAX233; DIL20
IC101, IC201, IC301, IC401, IC501, IC601: FT232RL; SSOP28DB
ICSP: AVR_SPI_PRG_6PTH; 2X3
L1: BL02RN1
LED1: LED-2COLOUR; LED3MM
LED101, LED201, LED301, LED401, LED501, LED601: Yellow; LED3MM_LARGEHOLES
LOGO1: OSHW-LOGOS; OSHW-LOGO-S
MODE: 10-XX; B3F-10XX
PC: M03PTH; 1X03
R1, R101, R102, R201, R202, R301, R302, R401, R402, R501, R502, R601, R602: 10K; AXIAL-0.4
R2, R103, R203, R303, R403, R503, R603: 1K; AXIAL-0.4
RST: 10-XX; B3F-10XX
TP1: M02PTH; 1X02
TP2: M01PTH; 1X01
USBA: USB-B; USB-B-PTH
USBB: USB-B; USB-B-PTH
USBC: USB-B; USB-B-PTH
USBD: USB-B; USB-B-PTH
USBE: USB-B; USB-B-PTH
USBF: USB-B; USB-B-PTH

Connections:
CRO: IC1.28 (PC5(ADC5/SCL)), TP2.1
GND: C1.2, C2.1, C3.2 (-), C4.2, C5.2, C6.2, C101.2, C102.2, C103.2, C201.2, C202.2, C203.2, C301.2, C302.2, C303.2, C401.2, C402.2, C403.2, C501.2, C502.2, C503.2, C601.2, C602.2, C603.2, IC1.8 (GND), IC1.22 (GND), IC2.6 (GND), IC2.9 (GND), IC101.7 (GND1), IC101.18 (GND2), IC101.21 (GND3), IC101.25 (AGND), IC101.26 (TEST), IC201.7 (GND1), IC201.18 (GND2), IC201.21 (GND3), IC201.25 (AGND), IC201.26 (TEST), IC301.7 (GND1), IC301.18 (GND2), IC301.21 (GND3), IC301.25 (AGND), IC301.26 (TEST), IC401.7 (GND1), IC401.18 (GND2), IC401.21 (GND3), IC401.25 (AGND), IC401.26 (TEST), IC501.7 (GND1), IC501.18 (GND2), IC501.21 (GND3), IC501.25 (AGND), IC501.26 (TEST), IC601.7 (GND1), IC601.18 (GND2), IC601.21 (GND3), IC601.25 (AGND), IC601.26 (TEST), ICSP.6, MODE.3, MODE.4 (P1), PC.1, R102.P$2 (2), R202.P$2 (2), R302.P$2 (2), R402.P$2 (2), R502.P$2 (2), R602.P$2 (2), RST.3, RST.4 (P1), USBA.GND, USBB.GND, USBC.GND, USBD.GND, USBE.GND, USBF.GND
MISO: IC1.18 (PB4(MISO)), ICSP.1, R2.P$1 (1)
MOSI: IC1.17 (PB3(MOSI/OC2)), ICSP.4, MODE.1 (S), MODE.2 (S1)
unnamed: C201.1, IC201.15 (USBDP), USBB.D+
unnamed: C202.1, IC201.16 (USBDM), USBB.D-
unnamed: IC201.19 (_RESET), R201.P$2 (2), R202.P$1 (1)
unnamed: LED201.A, R203.P$2 (2)
unnamed: IC201.23 (CBUS0), LED201.K (C)
unnamed: C401.1, IC401.15 (USBDP), USBD.D+
unnamed: C402.1, IC401.16 (USBDM), USBD.D-
unnamed: IC2.10 (C2-), IC2.16 (C2-)
unnamed: C2.2, L1.2, TP1.2
unnamed: IC2.11 (C2+), IC2.15 (C2+)
unnamed: IC2.12 (V-), IC2.17 (V-)
unnamed: IC401.19 (_RESET), R401.P$2 (2), R402.P$1 (1)
unnamed: LED401.A, R403.P$2 (2)
unnamed: IC401.23 (CBUS0), LED401.K (C)
unnamed: C301.1, IC301.15 (USBDP), USBC.D+
unnamed: C302.1, IC301.16 (USBDM), USBC.D-
unnamed: R201.P$1 (1), USBB.VBUS
unnamed: IC301.19 (_RESET), R301.P$2 (2), R302.P$1 (1)
unnamed: LED301.A, R303.P$2 (2)
unnamed: IC301.23 (CBUS0), LED301.K (C)
unnamed: R301.P$1 (1), USBC.VBUS
unnamed: C101.1, IC101.15 (USBDP), USBA.D+
unnamed: C102.1, IC101.16 (USBDM), USBA.D-
unnamed: IC101.19 (_RESET), R101.P$2 (2), R102.P$1 (1)
unnamed: LED101.A, R103.P$2 (2)
unnamed: IC101.23 (CBUS0), LED101.K (C)
unnamed: R401.P$1 (1), USBD.VBUS
unnamed: C501.1, IC501.15 (USBDP), USBE.D+
unnamed: C502.1, IC501.16 (USBDM), USBE.D-
unnamed: IC501.19 (_RESET), R501.P$2 (2), R502.P$1 (1)
unnamed: LED501.A, R503.P$2 (2)
unnamed: IC501.23 (CBUS0), LED501.K (C)
unnamed: R501.P$1 (1), USBE.VBUS
unnamed: C601.1, IC601.15 (USBDP), USBF.D+
unnamed: C602.1, IC601.16 (USBDM), USBF.D-
unnamed: IC601.19 (_RESET), R601.P$2 (2), R602.P$1 (1)
unnamed: LED601.A, R603.P$2 (2)
unnamed: IC601.23 (CBUS0), LED601.K (C)
unnamed: R601.P$1 (1), USBF.VBUS
unnamed: LED1.A, R2.P$2 (2)
RESET: C1.1, IC1.1 (PC6(/RESET)), ICSP.5, R1.P$2 (2), RST.1 (S), RST.2 (S1)
RX: IC2.4 (R1IN), PC.3
RXA: IC1.5 (PD3(INT1)), IC101.5 (RXD)
RXB: IC1.11 (PD5(T1)), IC201.5 (RXD)
RXC: IC1.13 (PD7(AIN1)), IC301.5 (RXD)
RXD: IC1.15 (PB1(OC1A)), IC401.5 (RXD)
RXE: IC1.23 (PC0(ADC0)), IC501.5 (RXD)
RXF: IC1.25 (PC2(ADC2)), IC601.5 (RXD)
RXS: IC1.2 (PD0(RXD)), IC2.3 (R1OUT)
SCK: IC1.19 (PB5(SCK)), ICSP.3, LED1.K (C)
TX: IC2.5 (T1OUT), PC.2
TXA: IC1.4 (PD2(INT0)), IC101.1 (TXD)
TXB: IC1.6 (PD4(XCK/T0)), IC201.1 (TXD)
TXC: IC1.12 (PD6(AIN0)), IC301.1 (TXD)
TXD: IC1.14 (PB0(ICP)), IC401.1 (TXD)
TXE: IC1.16 (PB2(SS/OC1B)), IC501.1 (TXD)
TXF: IC1.24 (PC1(ADC1)), IC601.1 (TXD)
TXS: IC1.3 (PD1(TXD)), IC2.2 (T1IN)
VBUSA: L1.1, R101.P$1 (1), USBA.VBUS
VCC: C3.1 (+), C4.1, C5.1, C6.1, C103.1, C203.1, C303.1, C403.1, C503.1, C603.1, IC1.7 (VCC), IC1.20 (AVCC), IC2.7 (VCC), IC101.4 (VCCIO), IC101.20 (VCC), IC201.4 (VCCIO), IC201.20 (VCC), IC301.4 (VCCIO), IC301.20 (VCC), IC401.4 (VCCIO), IC401.20 (VCC), IC501.4 (VCCIO), IC501.20 (VCC), IC601.4 (VCCIO), IC601.20 (VCC), ICSP.2, R1.P$1 (1), R103.P$1 (1), R203.P$1 (1), R303.P$1 (1), R403.P$1 (1), R503.P$1 (1), R603.P$1 (1), TP1.1

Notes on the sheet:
This design is released under the Creative Commons Attribution-ShareAlike 4.0 International License (CC BY-SA)

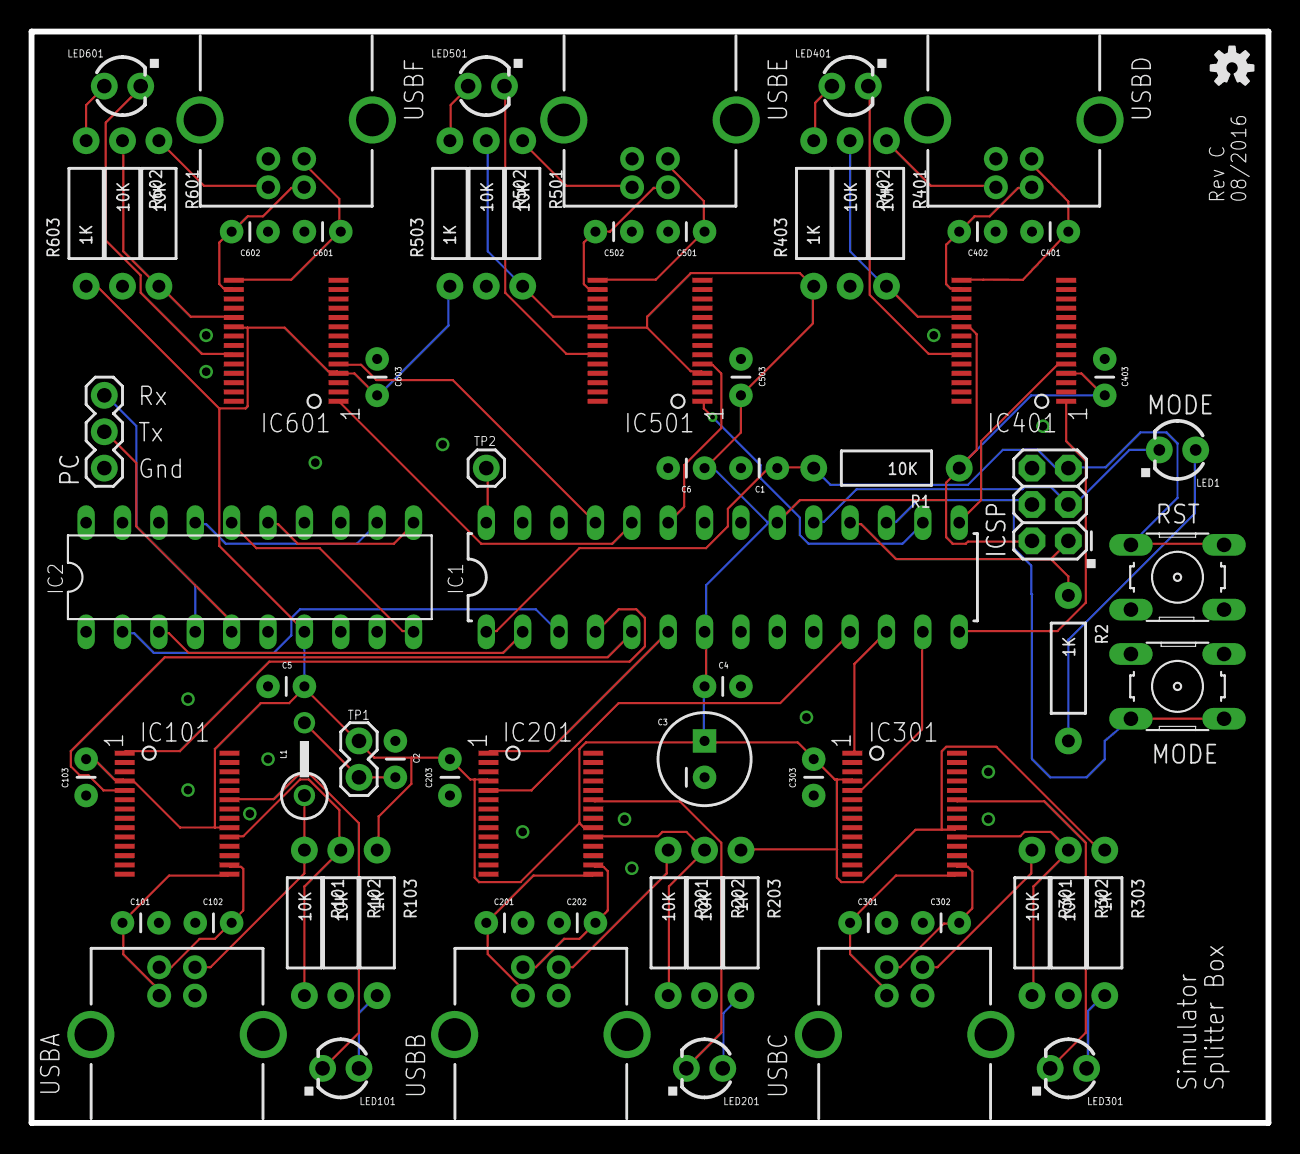
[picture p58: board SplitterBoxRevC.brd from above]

Board: 2 copper layers, 86.4 x 76.2 mm, 73 parts (0 on the bottom side), 64 nets.

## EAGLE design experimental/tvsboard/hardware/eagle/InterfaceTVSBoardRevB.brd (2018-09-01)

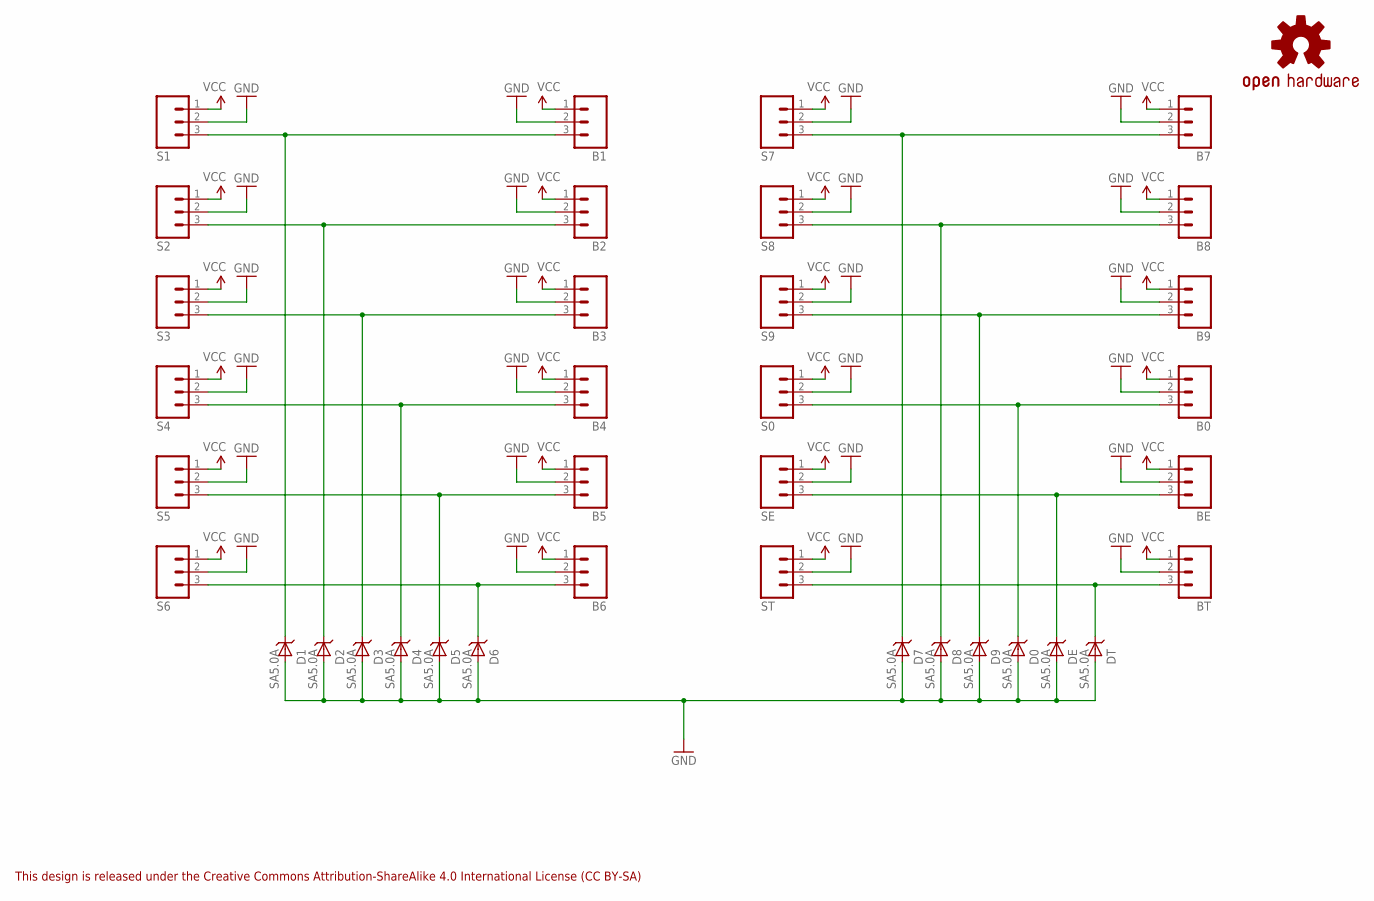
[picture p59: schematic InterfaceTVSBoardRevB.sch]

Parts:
B0, B1, B2, B3, B4, B5, B6, B7, B8, B9: M03PTH; 1X03
BE: M03PTH; 1X03
BT: M03PTH; 1X03
D0, D1, D2, D3, D4, D5, D6, D7, D8, D9: SA5.0A; DO41_TVS_UNI
DE: SA5.0A; DO41_TVS_UNI
DT: SA5.0A; DO41_TVS_UNI
LOGO1: OSHW-LOGOS; OSHW-LOGO-S
S0, S1, S2, S3, S4, S5, S6, S7, S8, S9: M03PTH; 1X03
SE: M03PTH; 1X03
ST: M03PTH; 1X03

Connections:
GND: B0.2, B1.2, B2.2, B3.2, B4.2, B5.2, B6.2, B7.2, B8.2, B9.2, BE.2, BT.2, D0.ANODE, D1.ANODE, D2.ANODE, D3.ANODE, D4.ANODE, D5.ANODE, D6.ANODE, D7.ANODE, D8.ANODE, D9.ANODE, DE.ANODE, DT.ANODE, S0.2, S1.2, S2.2, S3.2, S4.2, S5.2, S6.2, S7.2, S8.2, S9.2, SE.2, ST.2
unnamed: B1.3, D1.CATHODE, S1.3
unnamed: B2.3, D2.CATHODE, S2.3
unnamed: B3.3, D3.CATHODE, S3.3
unnamed: B4.3, D4.CATHODE, S4.3
unnamed: B5.3, D5.CATHODE, S5.3
unnamed: B6.3, D6.CATHODE, S6.3
unnamed: B7.3, D7.CATHODE, S7.3
unnamed: B8.3, D8.CATHODE, S8.3
unnamed: B9.3, D9.CATHODE, S9.3
unnamed: B0.3, D0.CATHODE, S0.3
unnamed: BE.3, DE.CATHODE, SE.3
unnamed: BT.3, DT.CATHODE, ST.3
VCC: B0.1, B1.1, B2.1, B3.1, B4.1, B5.1, B6.1, B7.1, B8.1, B9.1, BE.1, BT.1, S0.1, S1.1, S2.1, S3.1, S4.1, S5.1, S6.1, S7.1, S8.1, S9.1, SE.1, ST.1

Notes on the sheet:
This design is released under the Creative Commons Attribution-ShareAlike 4.0 International License (CC BY-SA)

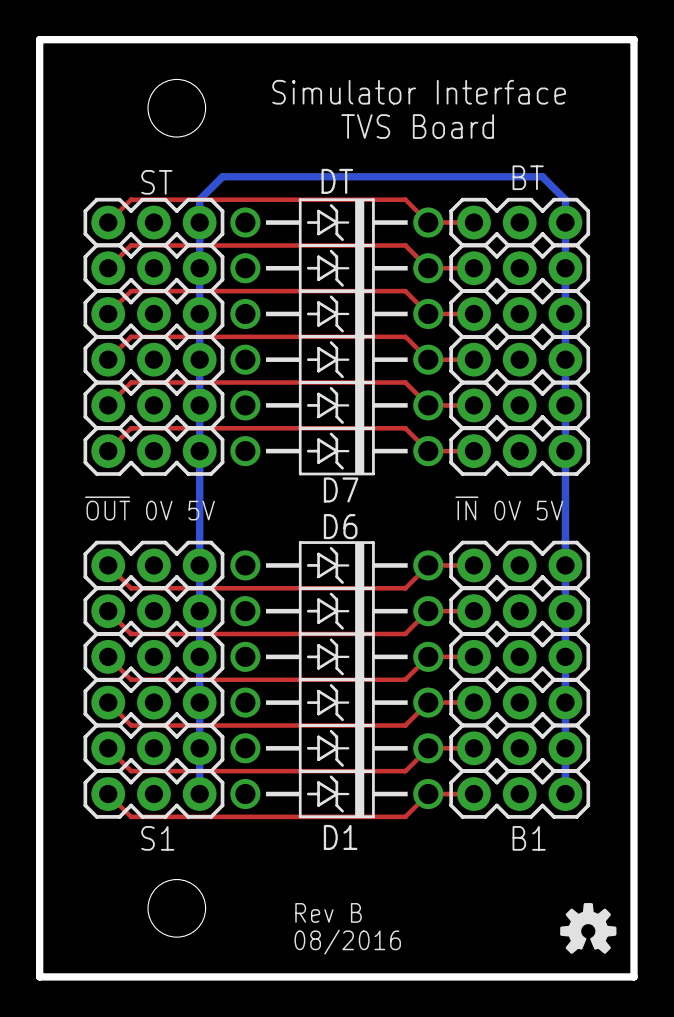
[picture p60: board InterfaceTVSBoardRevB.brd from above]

Board: 2 copper layers, 33.0 x 52.1 mm, 37 parts (0 on the bottom side), 14 nets.

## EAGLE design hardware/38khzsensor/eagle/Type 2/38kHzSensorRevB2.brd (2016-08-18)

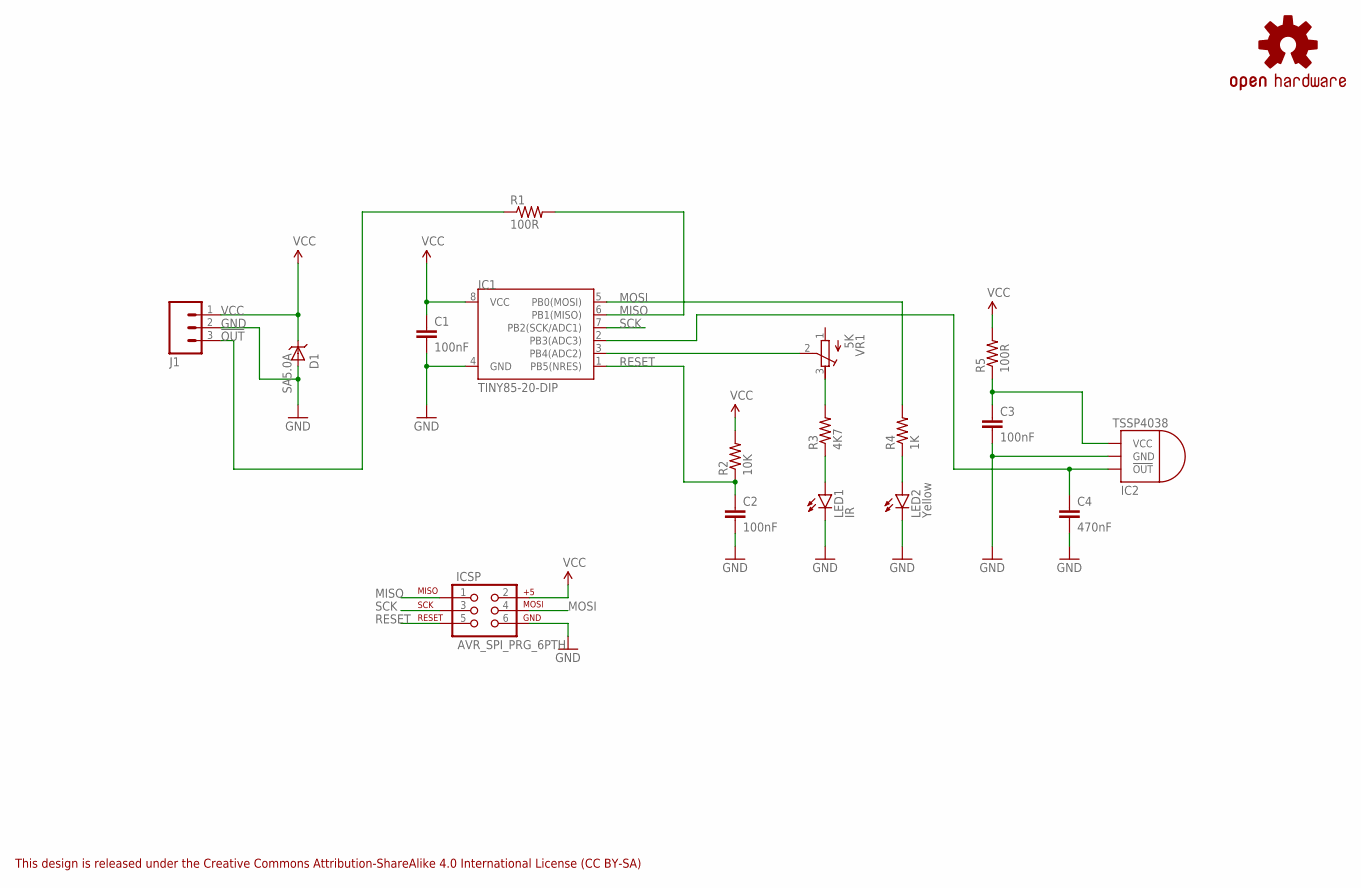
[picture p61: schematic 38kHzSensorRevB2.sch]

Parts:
C1, C2, C3: 100nF; CAP-PTH-SMALL
C4: 470nF; CAP-PTH-5MM
D1: SA5.0A; DO41_TVS_UNI
IC1: TINY85-20-DIP; DIP08
IC2: TSSP4038EDGE; TSSP4038_PKG_EDGE
ICSP: AVR_SPI_PRG_6PTH; 2X3
J1: M03PTH; 1X03
LED1: IR; LED5MM
LED2: Yellow; LED3MM
LOGO1: OSHW-LOGOS; OSHW-LOGO-S
R1, R5: 100R; AXIAL-0.4
R2: 10K; AXIAL-0.4
R3: 4K7; AXIAL-0.4
R4: 1K; AXIAL-0.4
VR1: 5K; RTRIM3296X

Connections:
!OUT: J1.3, R1.P$1 (1)
GND: C1.2, C2.2, C3.2, C4.2, D1.ANODE, IC1.4 (GND), IC2.GND, ICSP.6, J1.2, LED1.K (C), LED2.K (C)
MISO: IC1.6 (PB1(MISO)), ICSP.1, R1.P$2 (2)
MOSI: IC1.5 (PB0(MOSI)), ICSP.4, R4.P$2 (2)
unnamed: IC1.3 (PB4(ADC2)), VR1.2 (S)
unnamed: R3.P$2 (2), VR1.3 (E)
unnamed: C4.1, IC1.2 (PB3(ADC3)), IC2.OUT (!OUT)
unnamed: C3.1, IC2.VCC, R5.P$1 (1)
unnamed: LED1.A, R3.P$1 (1)
unnamed: LED2.A, R4.P$1 (1)
RESET: C2.1, IC1.1 (PB5(NRES)), ICSP.5, R2.P$1 (1)
SCK: IC1.7 (PB2(SCK/ADC1)), ICSP.3
VCC: C1.1, D1.CATHODE, IC1.8 (VCC), ICSP.2, J1.1, R2.P$2 (2), R5.P$2 (2)

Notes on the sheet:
This design is released under the Creative Commons Attribution-ShareAlike 4.0 International License (CC BY-SA)

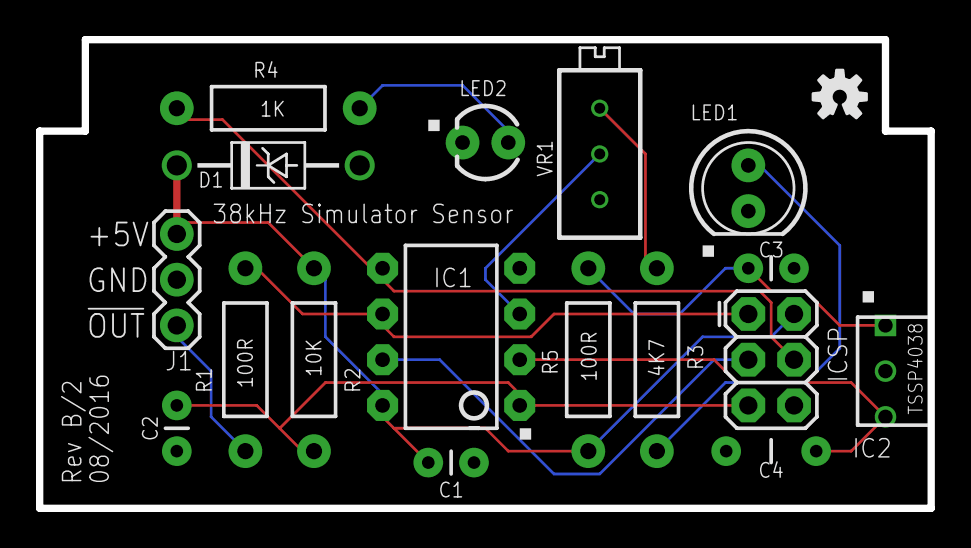
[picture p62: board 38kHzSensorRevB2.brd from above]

Board: 2 copper layers, 49.5 x 26.0 mm, 18 parts (0 on the bottom side), 13 nets.

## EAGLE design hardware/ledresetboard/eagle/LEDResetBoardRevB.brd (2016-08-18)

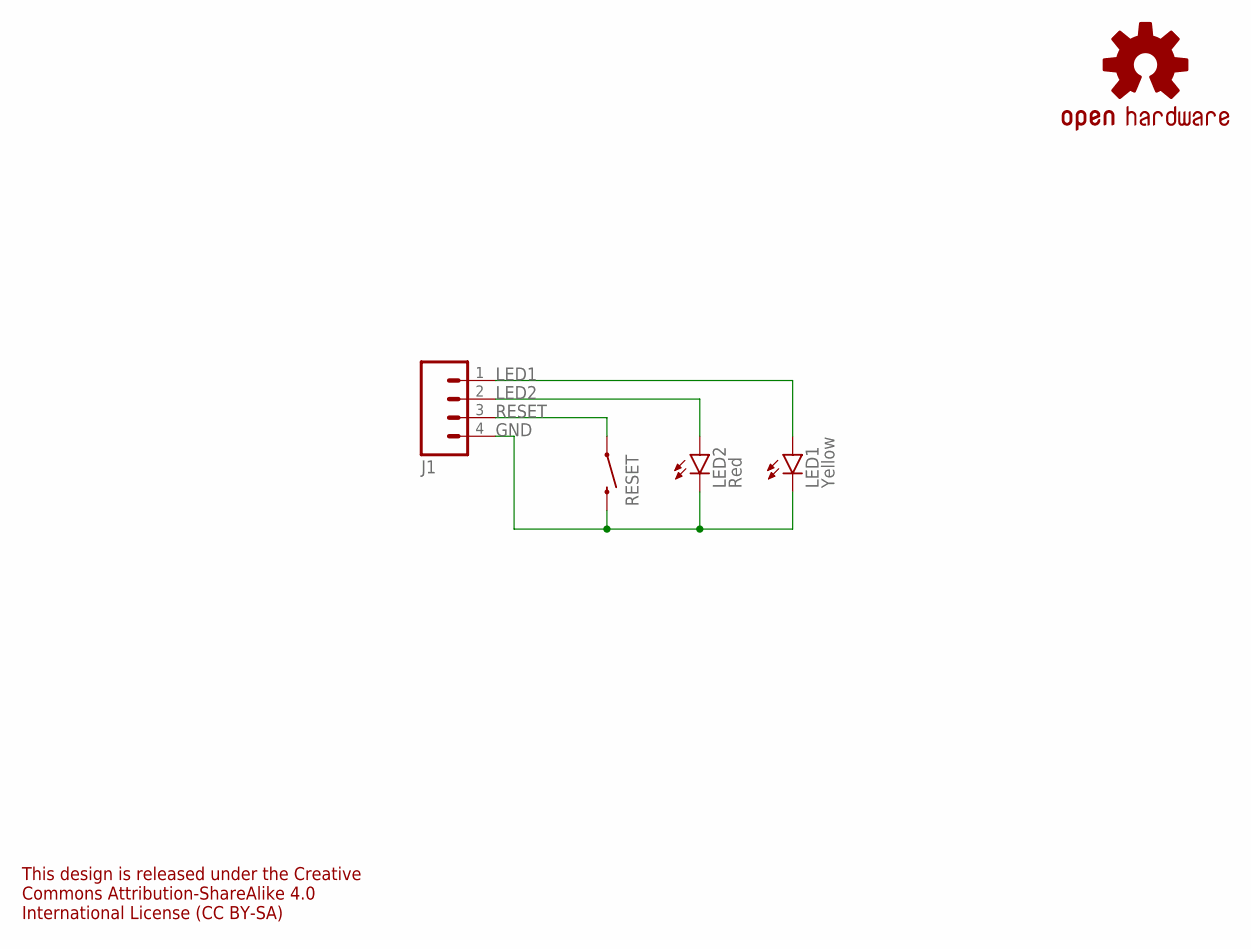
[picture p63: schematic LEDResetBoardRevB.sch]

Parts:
J1: M04PTH; 1X04
LED1: Yellow; LED3MM
LED2: Red; LED3MM
LOGO1: OSHW-LOGOS; OSHW-LOGO-S
RESET: SWITCH-MOMENTARY-2PTH; TACTILE-PTH

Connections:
GND: J1.4, LED1.K (C), LED2.K (C), RESET.3 (2)
LED1: J1.1, LED1.A
LED2: J1.2, LED2.A
RESET: J1.3, RESET.1

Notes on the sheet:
This design is released under the Creative Commons Attribution-ShareAlike 4.0 International License (CC BY-SA)

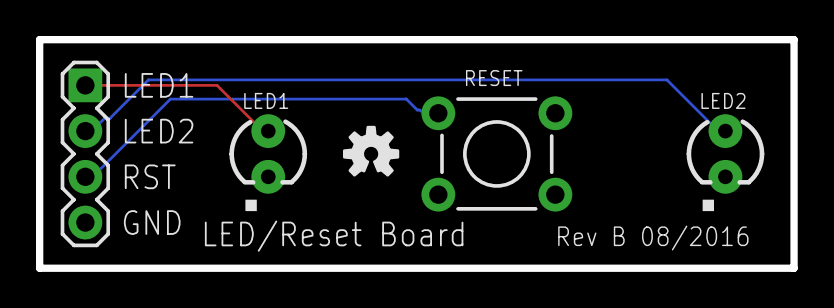
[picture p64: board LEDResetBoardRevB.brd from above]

Board: 2 copper layers, 41.9 x 12.7 mm, 5 parts (0 on the bottom side), 4 nets.

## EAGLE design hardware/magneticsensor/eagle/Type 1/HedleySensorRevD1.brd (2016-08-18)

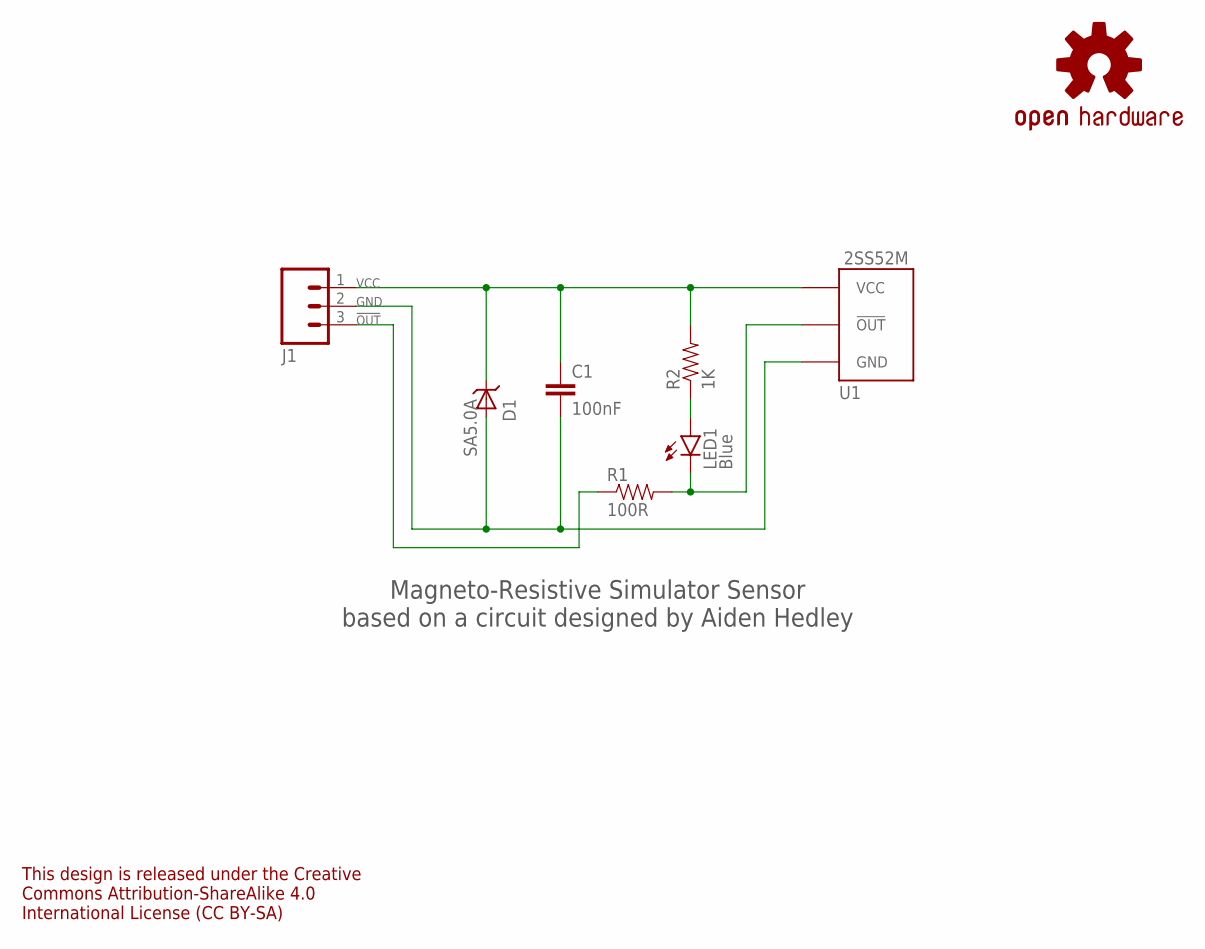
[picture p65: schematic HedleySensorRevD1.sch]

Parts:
C1: 100nF; CAP-PTH-SMALL
D1: SA5.0A; DO41_TVS_UNI
J1: M03PTH; 1X03
LED1: Blue; LED3MM
LOGO1: OSHW-LOGOS; OSHW-LOGO-S
R1: 100R; AXIAL-0.4
R2: 1K; AXIAL-0.4
U1: 2SS52MFLAT; 2SS52M_FLAT

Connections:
!OUT: J1.3, R1.P$1 (1)
GND: C1.2, D1.ANODE, J1.2, U1.P$1 (GND)
unnamed: LED1.K (C), R1.P$2 (2), U1.P$2 (!OUT!)
unnamed: LED1.A, R2.P$1 (1)
VCC: C1.1, D1.CATHODE, J1.1, R2.P$2 (2), U1.P$3 (VCC)

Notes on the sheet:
Magneto-Resistive Simulator Sensor based on a circuit designed by Aiden Hedley
This design is released under the Creative Commons Attribution-ShareAlike 4.0 International License (CC BY-SA)


Board: 2 copper layers, 49.5 x 26.0 mm, 8 parts (0 on the bottom side), 5 nets.

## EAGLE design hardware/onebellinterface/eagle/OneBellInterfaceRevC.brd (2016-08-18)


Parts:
C1, C2: 100uF; CPOL-RADIAL-100UF-25V
C3, C4, C5: 100nF; CAP-PTH-SMALL
D1: 1N4001; DO41_DIODE
D2: SA5.0A; DO41_TVS_UNI
IC1: 78L05; TO-92
IC2: MAX233; DIL20
IC3: TINY85-20-DIP; DIL08
ICSP: AVR_SPI_PRG_6PTH; 2X3
J1: M05PTH; 1X05
J2: M03PTH; 1X03
LED1: Red; LED3MM
LOGO1: OSHW-LOGOS; OSHW-LOGO-S
R1: 1K; AXIAL-0.4
R2: 10K; AXIAL-0.4

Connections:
GND: C1.2 (-), C2.2 (-), C3.2, C4.2, C5.2, D2.ANODE, IC1.2 (GND), IC2.6 (GND), IC2.9 (GND), IC3.4 (GND), ICSP.6, J1.1, J1.5, J2.2, LED1.K (C)
MISO: IC3.6 (PB1(MISO)), ICSP.1
MOSI: IC3.5 (PB0(MOSI)), ICSP.4, R1.P$2 (2)
unnamed: C1.1 (+), D1.C, IC1.3 (IN)
unnamed: LED1.A, R1.P$1 (1)
unnamed: IC2.11 (C2+), IC2.15 (C2+)
unnamed: IC2.10 (C2-), IC2.16 (C2-)
unnamed: IC2.12 (V-), IC2.17 (V-)
RESET: C5.1, IC3.1 (PB5(NRES)), ICSP.5, R2.P$1 (1)
RX: IC2.4 (R1IN), J1.3
RXD: IC2.3 (R1OUT), IC3.3 (PB4(ADC2))
SCK: IC3.7 (PB2(SCK/ADC1)), ICSP.3, J2.3
TX: IC2.5 (T1OUT), J1.4
TXD: IC2.2 (T1IN), IC3.2 (PB3(ADC3))
VCC: C2.1 (+), C3.1, C4.1, D2.CATHODE, IC1.1 (OUT), IC2.7 (VCC), IC3.8 (VCC), ICSP.2, J2.1, R2.P$2 (2)
VIN: D1.A, J1.2

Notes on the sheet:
This design is released under the Creative Commons Attribution-ShareAlike 4.0 International License (CC BY-SA)


Board: 2 copper layers, 49.5 x 26.0 mm, 17 parts (0 on the bottom side), 16 nets.

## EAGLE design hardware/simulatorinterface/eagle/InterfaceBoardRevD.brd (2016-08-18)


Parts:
B0, B1, B2, B3, B4, B5, B6, B7, B8, B9: M03PTH; 1X03
BE: M03PTH; 1X03
BT: M03PTH; 1X03
C1, C2: 100uF; CPOL-RADIAL-100UF-25V
C3, C4, C5, C6: 100nF; CAP-PTH-SMALL
D1: 1N4001; DO41_DIODE
D2: SA5.0A; DO41_TVS_UNI
FUSE: M02PTH; 1X02
IC1: 7805TV; TO220V
IC2: MAX233; DIL20
IC3: ATMEGA328P_PDIP; DIL28-3
ICSP: AVR_SPI_PRG_6PTH; 2X3
LED1: Yellow; LED3MM_LARGEHOLES
LED2: Red; LED3MM_LARGEHOLES
LOGO1: OSHW-LOGOS; OSHW-LOGO-S
PC: M05PTH; 1X05
R1: 10K; AXIAL-0.4
R2, R3: 1K; AXIAL-0.4
RST: M02PTH; 1X02
SLAVE: M02PTH; 1X02

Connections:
GND: B0.2, B1.2, B2.2, B3.2, B4.2, B5.2, B6.2, B7.2, B8.2, B9.2, BE.2, BT.2, C1.2 (-), C2.2 (-), C3.2, C4.2, C5.2, C6.2, D2.ANODE, IC1.2 (GND), IC2.6 (GND), IC2.9 (GND), IC3.8 (GND), IC3.22 (GND), ICSP.6, LED1.K (C), LED2.K (C), PC.1, PC.5, RST.2, SLAVE.2
MISO: B5.3, IC3.18 (PB4(MISO)), ICSP.1
MOSI: B4.3, IC3.17 (PB3(MOSI/OC2)), ICSP.4
unnamed: B7.3, IC3.23 (PC0(ADC0))
unnamed: B8.3, IC3.24 (PC1(ADC1))
unnamed: B9.3, IC3.25 (PC2(ADC2))
unnamed: B0.3, IC3.26 (PC3(ADC3))
unnamed: BT.3, IC3.28 (PC5(ADC5/SCL))
unnamed: BE.3, IC3.27 (PC4(ADC4/SDA))
unnamed: LED1.A, R2.P$2 (2)
unnamed: IC2.10 (C2-), IC2.16 (C2-)
unnamed: B3.3, IC3.16 (PB2(SS/OC1B))
unnamed: B2.3, IC3.15 (PB1(OC1A))
unnamed: B1.3, IC3.14 (PB0(ICP))
unnamed: IC2.11 (C2+), IC2.15 (C2+)
unnamed: IC2.12 (V-), IC2.17 (V-)
unnamed: D1.A, FUSE.1
unnamed: LED2.A, R3.P$2 (2)
unnamed: C1.1 (+), D1.C, IC1.1 (VI)
RESET: C6.1, IC3.1 (PC6(/RESET)), ICSP.5, R1.P$2 (2), RST.1
RX: IC2.4 (R1IN), PC.3
RXD: IC2.3 (R1OUT), IC3.2 (PD0(RXD))
SCK: B6.3, IC3.19 (PB5(SCK)), ICSP.3
SIG1: IC3.12 (PD6(AIN0)), R2.P$1 (1)
SIG2: IC3.13 (PD7(AIN1)), R3.P$1 (1)
TX: IC2.5 (T1OUT), PC.4
TX2: IC2.18 (T2OUT), SLAVE.1
TXD: IC2.1 (T2IN), IC2.2 (T1IN), IC3.3 (PD1(TXD))
VCC: B0.1, B1.1, B2.1, B3.1, B4.1, B5.1, B6.1, B7.1, B8.1, B9.1, BE.1, BT.1, C2.1 (+), C3.1, C4.1, C5.1, D2.CATHODE, IC1.3 (VO), IC2.7 (VCC), IC3.7 (VCC), IC3.20 (AVCC), ICSP.2, R1.P$1 (1)
VIN: FUSE.2, PC.2

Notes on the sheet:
This design is released under the Creative Commons Attribution-ShareAlike 4.0 International License (CC BY-SA)


Board: 2 copper layers, 61.0 x 52.1 mm, 34 parts (0 on the bottom side), 30 nets.

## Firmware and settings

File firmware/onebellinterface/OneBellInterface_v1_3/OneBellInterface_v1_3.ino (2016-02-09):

/*
One Bell Simulator Interface v1.3 Beta

Copyright 2014-2016 Andrew J Instone-Cowie.

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
Tested against Abel 3.9.1, Beltower 12.29 (2015) & Virtual Belfry 3.3.

	1.1 : One Bell version derived from Simulator Interface v2.2.
		Reduce code size heavily for One Bell version (8kB ATTiny85).
		Eliminate VTSerial (back to v1.7 cyclic code for option U, new code for option D).
		Implement SoftwareSerial and associated changes for ATTiny85 version
		Too many changes from main code to have a #define HW_ONEBELL!
		7,420 Bytes Flash, 215 Bytes SRAM.
		** 1st Manx Release (on Rev A PCB) - 20/05/2015 **
		Tested against Abel 3.9.1 (no code changes).
		Tested against Virtual Belfry 3.2 (no code changes).
	1.2 : Re-indent all the code with TestFX.
		Changed EEPROM handling to read-before-write to reduce EEPROM write wear, as per
		ATmel recommended practice.
		Amended recommended ATmega328P fuse settings.
		7,468 Bytes Flash, 215 Bytes SRAM
	1.3 : Update EEPROM handling code, simplified the CLI for setting simulator types (as
		option Q), and renamed the debounce timer command from U to B, consistent with main
		simulator interface code version 2.4.
		7,404 Bytes Flash, 222 Bytes SRAM.
	
*/

/*
Pins used on the ATTiny85 are as follows (physical package pins in brackets):
D0 (5) - LED
D2 (7) - Sensor Input
D3 (2) - Serial TX
D4 (3) - Serial RX
This minimises having hardwired connections to the ICSP pins. It is necessary to
unplug the IR sensor module from the PCB when programming the AVR.

ATTiny85 fuse settings for 8MHz internal clock:
low_fuses=0xe2
	SUT0
	CKSEL3
	CKSEL2
	CKSEL0
high_fuses=0xd5
	SPIEN
	EESAVE
	BODLEVEL1
extended_fuses=0xFF
*/

// Include the free memory library, freeMemory() is called by dumpdata().
#include <MemoryFree.h>

// Include the SoftwareSerial library (no hardware UART on the ATTiny85).
#include <SoftwareSerial.h>

// Initialise the SoftwareSerial library.
SoftwareSerial mySerial(4, 3); // RX, TX

// Bell timers and other non-volatile data are stored in EEPROM. The locations are the
// same as the 12-bell simulator board, but some locations are not used in the One Bell
// implementation:
// Locations 0-11  : Bells 1-12 Delay Timers (in cs)
// Locations 12-15 : Reserved for future Bells 13-16 Delay Timers
// Location  16    : Accidental Status (#,b) - Not supported yet
// Location  17    : Simulator Type (A,B,R,X)
// Location  18    : Number of channels (bell pins) active & to be scanned - NOT USED
// Location  19    : Debounce Timer (in ms)
// Location  20    : Serial port speed (as an index into serialSpeeds[]) - NOT USED

#include <EEPROM.h>

// Software version
const int majorVersion = 1;
const int minorVersion = 3;

// -------------------------------------------------------------------------------------------
//                                    Core Simulator
// -------------------------------------------------------------------------------------------

// The number of input channels for the One Bell version, oddly enough, always equals 1.
// Note that the delay timers data structure is still set up for 12 bells, as the simulators
// send and expect 12-bell data.
int numChannels = 1;

// Define bell sensor input pin.
const int bellSensorPin = 2;

// Define the character sent on the serial port to the simulator software, as
// defined in the MBI interface specification. This is an ASCII character, and for the One
// Bell version is always '1'.
const char bellStrikeChar = '1';

// Set up a variable to store the last observed sensor status, so we can detect transitions
// in input state. This is important to avoid duplicated sensor signals. 
int bellSensorLastValue; //initialise in setup, and set LOW (see below)

// Set up an array of strike signal timer delays, one per bell. The data type is unsigned
// long, because these values will be added to the output of millis(). Note that this code
// does everything in millisenconds (as does Beltower), although the MBI interface and Abel
// define values in centiseconds.
unsigned long bellStrikeDelay[12]; // initialise these in setup()

// Set up a variable to hold the actual time of the next character is due to be sent. The
// data type is unsigned long, because these values will be the sum of bellStrikeDelay and
//the output of millis().
unsigned long bellCharSendTime; // initialise in setup()

// Set up a char to hold the current simulator type (Abel, Beltower, etc
char simulatorType; // initialised from EEPROM in setup. See option E.

// Define an array of valid simulator types for input checking.
// Abel/Beltower/Ringleader/Virtual Belfry/Generic. See also printSimulatorTypeName();
const char validSimulatorTypes[] = "ABRVX"; 

// -------------------------------------------------------------------------------------------
//                                   Sensor Debounce
// -------------------------------------------------------------------------------------------

// Set up a variable to hold the time that the debounce timer will expire. The data type is
// unsigned long, because these values will be the sum of bellDebounceDelay and the output
// of millis().
unsigned long bellDebounceEndTime; // initialise in setup()

// Set up a variable to hold the debounce delay time, in milliseconds.
unsigned long bellDebounceDelay ; // initialised from EEPROM in setup

// Define the maximum permitted debounce timer value. Current value is stored in EEPROM, so
// must be <=255 ms. This value is used when setting the timer via the U CLI option.
// The minDebounceTimer will always be 1ms, so no definition for it.
const unsigned long maxDebounceDelay = 20; //ms

// Define the default debounce timer value in case the EEPROM is not yet set sensibly.
const unsigned long defaultDebounceDelay = 4; //ms

// -------------------------------------------------------------------------------------------
//                                    State Machines
// -------------------------------------------------------------------------------------------

// Set up an integer variable to indicate whether the state machine is in the
// program state "WAIT_FOR_INPUT" (0), "WAIT_FOR_DEBOUNCE" (1), or "WAIT_TO_SEND"(2).
int bellMachineState; // initialise in setup()

// Define the possible machine states as text to make the code more readable.
#define WAIT_FOR_INPUT 0
#define WAIT_FOR_DEBOUNCE 1
#define WAIT_TO_SEND 2

// -------------------------------------------------------------------------------------------
//                                      Debugging
// -------------------------------------------------------------------------------------------
// Set up a Debug Mode flag - this always cleared on reset, so not held in EEPROM.
boolean debugMode = false;

// Set up a Debug Flags Mask variable. The first 4 bits (0-3) correspond to debugging
// facilities in the code (1=on, 0=off). This allows each facility to turned on and off
// independently. These can be changed on the fly with the D option.
int debugFlagsMask = 1; //debug starts with DEBUG_PULSE_TIMER flag set by default

// Define the maximum configured number of flags. This value will depend on the flags
// actually implemented in the code. Currently there are 3 flags, as #defined below.
// If you add a debug level, increment this constant so that the CLI works.
const int maxDebugFlags = 3;

// Define the debug flags as text to make the code more readable
#define DEBUG_PULSE_TIMER 1		//bit 0
#define DEBUG_SHOW_MISFIRES 2	//bit 1
#define DEBUG_SHOW_DEBOUNCE 4	//bit 2
// (See also the function printDebugFlagName(), seeing as F() is not available globally)

// Define the default debug deplay timer. See option Z.
const unsigned long defaultDelayTimer = 500;

// -------------------------------------------------------------------------------------------
//                                   Debug Pulse Timing
// -------------------------------------------------------------------------------------------

// These variables are used for debug mode pulse length timing and counting only. There is
// no need to do pulse timing during normal operation.

// Set up two variables to hold the actual start and end times of the sensor pulse.
// The data type is unsigned long, because the values will be the output of micros(). These
// are used in debug mode only to calculate the length of the (first) sensor pulse.
unsigned long pulseStartTime; // initialise in setup()
unsigned long pulseEndTime;   // initialise in setup()

// Set up a variable to store the last observed sensor status, so we can detect transitions.
// This is used for debug mode pulse timing only, because updating the real
// bellSensorLastValue would lose the debounce effect for real simulator operation (which
// has to carry on regardless).
int pulseTimeLastValue; //initialise in setup, and set LOW (see below)

// Set up an integer variable to count the pulses (to show how noisy a sensor is). We do this
// by counting spurious pulse *ends* (LOW to HIGH) when we aren't expecting them, and to make
// sure we timed only the first pulse.
int pulseTimeCount; //initialise in setup, and set to zero

// -------------------------------------------------------------------------------------------
//                                     Test Mode
// -------------------------------------------------------------------------------------------

// These variables are used for test mode. None of these things are configurable on the fly.

// Define the delay before test mode kicks in after selecting the "T" CLI option
const int testStartDelay = 20; //seconds

// Define the number of bells used in test mode
const int testBells = 12;

// Define the inter-bell interval used in test mode. 200ms equates to a 12-bell peal speed
// of 3h30m with an open handstroke lead.
const int testInterval = 200; //msec

// -------------------------------------------------------------------------------------------
//                                     LEDs & Timing
// -------------------------------------------------------------------------------------------

// Signal LED pin definition
const int LED = 0;

/*
*********************************************************************************************
*                                   Function setup()                                        *
*********************************************************************************************
*/

// the setup routine runs once on powerup or reset:
void setup() {   

	// initialize the LED pin as output and turn the LED off.
	pinMode( LED, OUTPUT );
	digitalWrite( LED, LOW );

	// Load default values from EEPROM
	loadFromEEPROM();

	// setup data structures

	// initialize the bell sensor digital input pin with the pullup resistor active.
	// The photohead pulls the pin LOW when there is a signal.
	pinMode( bellSensorPin, INPUT_PULLUP );

	// initialize the last sensor status for the bell. Set this initially
	// to be LOW, so that the very first pass of loop() doesn't find a spurious transition
	// if the bells are down (and thus signalling continuously) and result in a fire-up
	// on startup.
	bellSensorLastValue = LOW;
	
	// initialize the strike send time value. This value should never get used, because
	// it will be overwritten when the actual time is calculated as the state machine enters
	// "WAIT_TO_SEND".
	bellCharSendTime = millis();

	// initialize the debounce timer end time value. This value should never get used,
	// because it will be overwritten when the actual time is calculated as the state
	// machine leaves "WAIT_FOR_INPUT".
	bellDebounceEndTime = millis();

	// initialize the state machine flag. Starts by waiting for input.
	// Setting this to "WAIT_TO_SEND" would result in an immediate timer expiry for every
	// bell on the first pass of loop(), and another one row fire-up.
	bellMachineState = WAIT_FOR_INPUT;

	// initialise the variables used for debug mode pulse length measurements    
	pulseStartTime = micros();
	pulseEndTime = micros();
	pulseTimeLastValue = HIGH;
	pulseTimeCount = 0;
	
	// Set up the serial port. The MBI interface spec uses 2400 8N1. Note that SoftwareSerial
	// does not support the 2400_8N1 syntax.
	mySerial.begin( 2400 );
	mySerial.listen();
	// For compatibility with the MBI startup message - It's unclear whether any of the
	// simulators actually use this for anything.
	mySerial.println(F("<On.>"));

	// Announce the software version on startup or reset
	blinkLED( LED, majorVersion, minorVersion ); 

}

/*
*********************************************************************************************
*                                     Function loop()                                       *
*********************************************************************************************
*/

// once setup has completed, the loop routine runs over and over again forever:
void loop() {

	// main loop start, process the state machine. There is only one state machine in this
	// version, so there is no for loop here.

	// Variable to store the value read from the pin
	int bellSensorValue;
	
	switch ( bellMachineState ) {

		// ---------------------------------------------------------------------------------------
		// -                                 WAIT_FOR_INPUT                                      -
		// ---------------------------------------------------------------------------------------
	case WAIT_FOR_INPUT:

		// The bell is in "WAIT_FOR_INPUT" state
		// Read the value from the sensor pin
		bellSensorValue = digitalRead( bellSensorPin );
		
		if ( bellSensorValue == LOW && bellSensorLastValue == HIGH ) {
			
			// This is a HIGH to LOW transition since we last looked, so we have the start of a
			// sensor pulse. Note the current time in a scratch variable (to avoid calling
			// millis() twice)
			unsigned long timeNow;
			timeNow = millis();
			
			// Set the time that the character should be sent to the simulator to now + the delay
			// timer. (Do this calculation here so we only have to do the comparison in following
			// loops, not the addition)
			bellCharSendTime = timeNow + bellStrikeDelay[0]; //always delay[0] for the One Bell

			// Set the time that the debounce timer will expire to to now + the debounce timer.
			// (Do this calculation here so we only have to do the comparison in following loops,
			// not the addition)
			bellDebounceEndTime = timeNow + bellDebounceDelay;
			
			// Set the last observed value to the current state of the sensor, which is LOW.
			// For an explanation of why we do this, see below.
			bellSensorLastValue = bellSensorValue;

			// Use the LED to signal strikes on bell 1 (MBI always starts at bell 1, even for
			// <12 bells). Turn on when the pulse is received, off when character is sent. 
			digitalWrite( LED, HIGH );
			
			// Move the machine state on to "WAIT_FOR_DEBOUNCE"
			bellMachineState = WAIT_FOR_DEBOUNCE;
			
			// If we are in debug mode, grab the pulse start time and reset the counter.
			// Both the pulse timer and the misfire detection require pulse timing to be done
			if ( debugMode && isDebugFlagSet( DEBUG_PULSE_TIMER | DEBUG_SHOW_MISFIRES ) ) {
				
				pulseStartTime = micros();
				
				// Avoid overflows giving a silly number if we get to a debug print before the end
				// of the first pulse! A pulse length of 0 means the pulse has not ended yet.
				pulseEndTime = pulseStartTime;
				pulseTimeLastValue = bellSensorValue;
				pulseTimeCount = 0; //incremented at the END of the pulse
				
				// We only run this code at the start of a valid pulse. The counter is used
				// to ensure that we only measure the duration of the first pulse in a potential
				// string of noisy input pulses (which are ignored by the main interface code).
				
			} //debugMode
			
		}
		else // this is not the start of a pulse
		{

			// Set the last observed value to the current state of the sensor, which may
			// (still) be LOW or (by now) HIGH.
			bellSensorLastValue = bellSensorValue;
			
			// We stay in the "WAIT_FOR_INPUT" state. We may have come back here and found the
			// sensor still LOW after sending the character to the simulator if the delay is
			// very short and the pulse very long, hence the transition detection.
			
		} //bellSensorValue
		
		break; //bellMachineState == WAIT_FOR_INPUT

		// ---------------------------------------------------------------------------------------
		// -                                WAIT_FOR_DEBOUNCE                                    -
		// ---------------------------------------------------------------------------------------      
	case WAIT_FOR_DEBOUNCE:
		
		// The bell is in "WAIT_FOR_DEBOUNCE" state.
		// Check whether the signal has ended too soon (and so is considered noise).
		
		// Read the value from the sensor pin
		bellSensorValue = digitalRead( bellSensorPin );
		
		if ( bellSensorValue == HIGH ) {
			
			// Input has gone high again, pulse was too short, so this is a misfire.
			
			// Turn the LED off again if it was on
			digitalWrite( LED, LOW );
			
			// Set the machine state back to "WAIT_FOR_INPUT"
			bellMachineState = WAIT_FOR_INPUT;
			
			// If we are in a debug mode, report the misfire and pulse data.
			if ( debugMode && isDebugFlagSet( DEBUG_SHOW_MISFIRES ) ) {
				
				// Grab the time of the end of the pulse (approximately) 
				pulseEndTime = micros();
				
				mySerial.print( bellStrikeChar );
				mySerial.print(F(" "));
				mySerial.print( bellCharSendTime );
				mySerial.print(F(" M " ));
				mySerial.println( pulseEndTime - pulseStartTime );
				
				// There is no need to set the pulse counter here - misfires are by
				// definition pulse #1 of 1. There may however be noise pulses *after*
				// the first one which is longer than the debounce timer, so we will
				// update the pulse counter when in WAIT_TO_SEND
				
			} //debugMode
			
		}
		else if ( millis() >= bellDebounceEndTime )
		{
			
			// Input is still low (otherwise we would have bailed out in the clause above)
			// and the debounce timer has now expired, so we have a good signal at least 
			// bellDebounceDelay ms long. Move the machine on to WAIT_TO_SEND state.
			bellMachineState = WAIT_TO_SEND;
			
			// Note that with SoftwareSerial, writes are blocking (there being no UART
			// write buffer), so each character written takes ~4ms to process. If
			// DEBUG_SHOW_DEBOUNCE is set, this will set an artificial floor of ~30ms on the
			// value of DEBUG_PULSE_TIMER output, as we don't grab the pulse end time until we
			// are in WAIT_TO_SEND. This is an issue only for debugging output.
			
			if ( debugMode && isDebugFlagSet( DEBUG_SHOW_DEBOUNCE ) ) {
				mySerial.print( bellStrikeChar);
				mySerial.print(F(" "));
				mySerial.print( bellCharSendTime );
				mySerial.println(F(" D" ));
			} //debugMode		 
			
		}
		
		// There is no other else here - if the input is still low and the timer
		// has not expired, we are still testing the signal quality so we just loop round.
		
		break; // bellMachineState == WAIT_FOR_DEBOUNCE

		// ---------------------------------------------------------------------------------------
		// -                                    WAIT_TO_SEND                                     -
		// ---------------------------------------------------------------------------------------      
	case WAIT_TO_SEND:
		
		// The bell is in "WAIT_TO_SEND" state.

		// We don't read the sensor pin at all when in this state. This debounces the input
		// and ignores spurious input. However there is a weakness here: If the delay is
		// insanely long (the protocol supports up to 0xFE (254) centiseconds (Abel allows
		// values up to 250cs (0xFA) or 2550ms to be input, Beltower allows values up to 2550ms
		// (in 10ms increments) (0xFF)), then there is the possibility that signals may be
		// lost. This has not been addressed here, as it means having more than one signal
		// outstanding for a single bell, and a queue of timers, and this behaviour is not
		// representative of the behaviour of real bells...
		
		// Check the timer - has it expired?
		if ( millis() >= bellCharSendTime ) {
			
			// Timer has expired, send the appropriate character to the interface. This uses
			// Serial.print because the MBI protocol specifies ASCII characters for bell strike
			// signals. (The serial command code uses Serial.write because it sends raw bytes.)
			
			// If any debug mode is set, suppress the normal output altogether. Debug code
			// supplies its own output as needed
			if ( ! debugMode ) {
				mySerial.print( bellStrikeChar );
			}
			
			// Turn the LED off again if appropriate
			digitalWrite( LED, LOW );
			
			// Set the machine state back to "WAIT_FOR_INPUT"
			bellMachineState = WAIT_FOR_INPUT;       
			
			// If we are in debug, send the timer values. This could be logged to a file for
			// later analysis.
			if ( debugMode ) {
				
				if ( isDebugFlagSet( DEBUG_PULSE_TIMER ) ) {
					
					mySerial.print( bellStrikeChar );
					mySerial.print(F(" "));
					mySerial.print( bellCharSendTime );
					mySerial.print(F(" S "));
					mySerial.print( pulseEndTime - pulseStartTime );
					mySerial.print(F(" "));
					mySerial.println(pulseTimeCount);
					
					// Reset the pulse counter, as we are going back to WAIT_FOR_INPUT
					pulseTimeCount = 0;
				}

			} //debugMode
			
		} //timer expired
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

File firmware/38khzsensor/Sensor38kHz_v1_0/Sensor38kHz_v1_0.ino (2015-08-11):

// Simple firmware for prototype 38kHz Sensors

// Use 8MHz internal clock

#define PIN_PWM 4     // IR LED - chip leg 3
#define PIN_DETECT 3  // IR Sensor - chip leg 2
#define PIN_STATUS 0  // Yellow LED - chip leg 5
#define PIN_OUTPUT 1  // Interface Output - chip leg 6


void setup()
{

  // Set up pins 
  pinMode(PIN_DETECT, INPUT_PULLUP);
  pinMode(PIN_STATUS, OUTPUT);
  pinMode(PIN_OUTPUT, OUTPUT);
  pinMode(PIN_PWM, OUTPUT);

  digitalWrite(PIN_STATUS, LOW);  // LED off
  digitalWrite(PIN_OUTPUT, HIGH); // Output off
  digitalWrite(PIN_PWM, LOW); // When not sending PWM, we want it low

  // Power-up signal on the LED
  digitalWrite(PIN_STATUS, HIGH);
  delay(250);
  digitalWrite(PIN_STATUS, LOW);
  delay(250);
  digitalWrite(PIN_STATUS, HIGH);
  delay(250);
  digitalWrite(PIN_STATUS, LOW);

  // Timer 1 Setup - 38kHz PWM, 25% Duty Cycle
  // Check against data sheet
  TCCR1 = _BV (CS10);           // no prescaler
  GTCCR = _BV (COM1B1) | _BV (PWM1B);  //  clear OC1B on compare
  OCR1B = 52;                   // duty cycle (25%)
  OCR1C = 210;                  // frequency 38kHz

}

void loop() {

  // Read the state of the IR sensor pin, track that state on the output pin,
  // and (inverted) on the LED.
  digitalWrite(PIN_OUTPUT, digitalRead(PIN_DETECT));
  // NB reading the *output* pin, set the LED to be the opposite.
  digitalWrite(PIN_STATUS, !digitalRead(PIN_OUTPUT));

}

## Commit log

2015-05-25 Simulator Interface
    [InterfaceBoardRevB.brd, InterfaceBoardRevB.sch, LEDResetBoardRevA.brd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]
2015-08-05 Adding One Bell Interface
    Documentation v1.0 and firmware files v1.1 for the One Bell Simulator
    Interface added.
    [OneBellInterfaceRevA.brd, OneBellInterfaceRevA.sch]
2015-08-11 Added sensor designs
    Added designs and documentation for standard IR, magneto-resistive and
    experimental IR sensors.
    [38kHzSensorRevA1.brd, 38kHzSensorRevA1.sch, 38kHzSensorRevA2.brd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]
2015-08-16 Fix debounce timer value
2015-08-16 Add Rev C magneto-resistive sensor as option
    Document the use of the Rev C M-R sensor board as an alternative to the
    infra-red sensor for the one bell simulator interface.
2015-10-30 Updated AVR fuse settings
    Updated AVR fuses to re-enabled BOD at Level 1 (2.7V)
2015-11-11 Added custom Eagle library
    Added an Eagle library of customised and adapted parts which may be
    required by some PCB CAD files.
2015-12-08 Splitter Box first prototype
    Functional prototype of a USB Splitter Box, to allow one simulator
    interface to drive multiple simulator PCs independently.
    [FP1 Parts List.xlsx, SplitterBoxRevA.brd, SplitterBoxRevA.sch]
2016-01-28 Added SimulatorInterface_v2_4
    Add ability to disable individual sensors e.g. to bypass a faulty
    sensor, by means of a new state machine state SENSOR_DISABLED (option
    E). Update much of the EEPROM handling code, added locations to make
    enabled sensors and debug masks persistent. Code cleanup, remove a lot
    of hard coded constants. Some values remain fixed at 12 because of the
    hardware config or the MBI protocol spec. Changed the way the # option
    works, to give a better CLI on interfaces with <12 channels equipped.
    Simplified the CLI for setting simulator types (as option Q), and
    renamed the debounce timer command from U to B.
    13,508 Bytes Flash, 631
    Bytes SRAM.
    [CLI_Functions.ino, Debug_Functions.ino, EEPROM_Functions.ino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]
2016-01-31 Debug Bugfix
    Stop disabling already disabled debugging
    [CLI_Functions.ino, EEPROM_Functions.ino, SimulatorInterface_v2_4.ino]
2016-01-31 New development version OneBellInterface_v1_3
    Update EEPROM handling code, simplified the CLI for setting simulator
    types (as option Q), and renamed the debounce timer command from U to B,
    consistent with main simulator interface code version 2.4.7,404 Bytes
    Flash, 222 Bytes SRAM.
2016-01-31 Consolidated boards.txt
    Single consolidated boards.txt file for all simulator boards
2016-02-11 Minor bugfix
    Rationalise LED diagnostic codes
    [CLI_Functions.ino, LED_Functions.ino, SimulatorInterface_v2_4.ino]
2016-02-11 Minor CLI bugfix
    Fixed spurious CLI input echo.
    [CLI_Functions.ino]
2016-04-13 Added magnet mountings
    Added details of simple magnet mountings for magneto-resistive sensors.
2016-04-24 Minor layout changes for SeeedStudio
    Improved a few track clearances on the Simulator Interface and One Bell
    Interface PCBs to pass SeeedStudio's standard DRC, updated Gerbers for
    both OSH Park and SeeedStudio fabricators.
    [InterfaceBoardRevC.brd, InterfaceBoardRevC.sch, OneBellInterfaceRevB.brd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]
2016-05-12 Minor updates.
    Refresh Gerbers, OSH Park and SeeedStudio versions for all production
    boards, remove old code versions.
    [InterfaceBoardRevB.brd, InterfaceBoardRevB.sch, OneBellInterfaceRevA.brd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]
2016-05-12 Updated docs with SeeedStudio details
    Details of alternative PCB manufacturer
2016-06-01 Add diagrams
    Added diagrams illustrating sensor positioning options.
2016-06-25 Installation updates
    Chirk & Liverpool now have experimental TVS boards.
2016-06-25 Experimental stuff
    Early versions of experimental TVS and twin-detector sensor boards.
    [InterfaceUSB6TVSBoard.brd, InterfaceUSB6TVSBoard.sch, TwinSensorTestRevB.brd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]
2016-06-26 Moved splitterbox to the experimental world
    Moved splitterbox to the experimental world, and added a couple more
    twin sensor images.
    [FP1 Parts List.xlsx, SplitterBoxRevA.brd, SplitterBoxRevA.sch]
2016-08-06 Add schematic
2016-08-11 Update Arduino boards
2016-08-13 Updated custom Eagle library
    Added a new package for a uni-directional TVS diode
2016-08-15 TVS component change
    First tranche of changes replacing the SA5.0CA bi-directional TVS diode
    with the SA5.0A uni-directional component.
    [38kHzSensorRevA1.brd, 38kHzSensorRevA1.sch, 38kHzSensorRevA2.brd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]
2016-08-15 Remove splitterbox
    Should be in the experimental heirarchy of the development branch only
    [FP1 Parts List.xlsx, SplitterBoxRevC.brd, SplitterBoxRevC.sch]
2016-08-18 Reinstate splitterbox
    Reinstate splitterbox to the development branch.
    [FP1 Parts List.xlsx, SplitterBoxRevC.brd, SplitterBoxRevC.sch]
2016-08-18 Tidy up experimental area
    [SplitterBoxRevC.brd, SplitterBoxRevC.sch]
2016-08-24 Twin Sensor Rev C
    Details of a simplified twin sensor board using an ATtiny85 MCU,
    avoiding the need to solder TQFPs. No diag port.
    [TwinSensorRevC.brd, TwinSensorRevC.sch, TwinSensorTestRevB.brd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]
2016-10-02 Update hardware directories for Arduino 1.6.12
    Reorganise and update the Arduino custom boards hardware directories,
    add build.board entries throughout.
2016-10-06 Updated boards files
    Consolidated hardware directory for all boards, no bootloader, tested
    against Arduino 1.6.12
2017-01-19 Documentation updates
    Arduino IDE to 1.6.12, Boards Manager, VB 3.4.
2017-03-01 Updated custom Eagle library
    New devices and packages
2025-05-03 Firmware 2.6
    Version of firmware for Type 1 simulators to provide facility to disable application of strike delays in the interface (i.e. Type 2 firmware behaviour). This version was developed for a specific use 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
2025-06-23 Swing Timer Backport
    Backport swing timer debug option from Type 2 firmware.
2025-07-01 Beltower 14.05
    Noted as tested against Beltower 14.05, which resolves Issue #8.
    [SimulatorInterface_v2_5.ino, SimulatorInterface_v2_6.ino]

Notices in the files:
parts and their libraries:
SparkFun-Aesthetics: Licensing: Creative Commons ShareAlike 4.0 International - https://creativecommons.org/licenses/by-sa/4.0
